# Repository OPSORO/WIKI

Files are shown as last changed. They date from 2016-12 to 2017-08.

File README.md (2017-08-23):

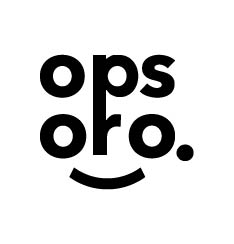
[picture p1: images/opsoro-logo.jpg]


# Welcome!

Welcome to the documentation wiki for OPSORO - open platform for social
robotics! This wiki is meant to guide you through the whole process of making
your own social robot(s).

* If you want more information about OPSORO, please visit our [website](https://www.opsoro.be/).
* If you have any questions, please visit our [forum](https://www.opsoro.be/forum/).
* You will find all necessary design files on our OPSORO [GitHub](https://github.com/OPSORO/) account.
* This wiki/book is licensed under the Creative Commons Attribution-ShareAlike 4.0 license.
* The OPSORO documentation was last updated in August 2017.

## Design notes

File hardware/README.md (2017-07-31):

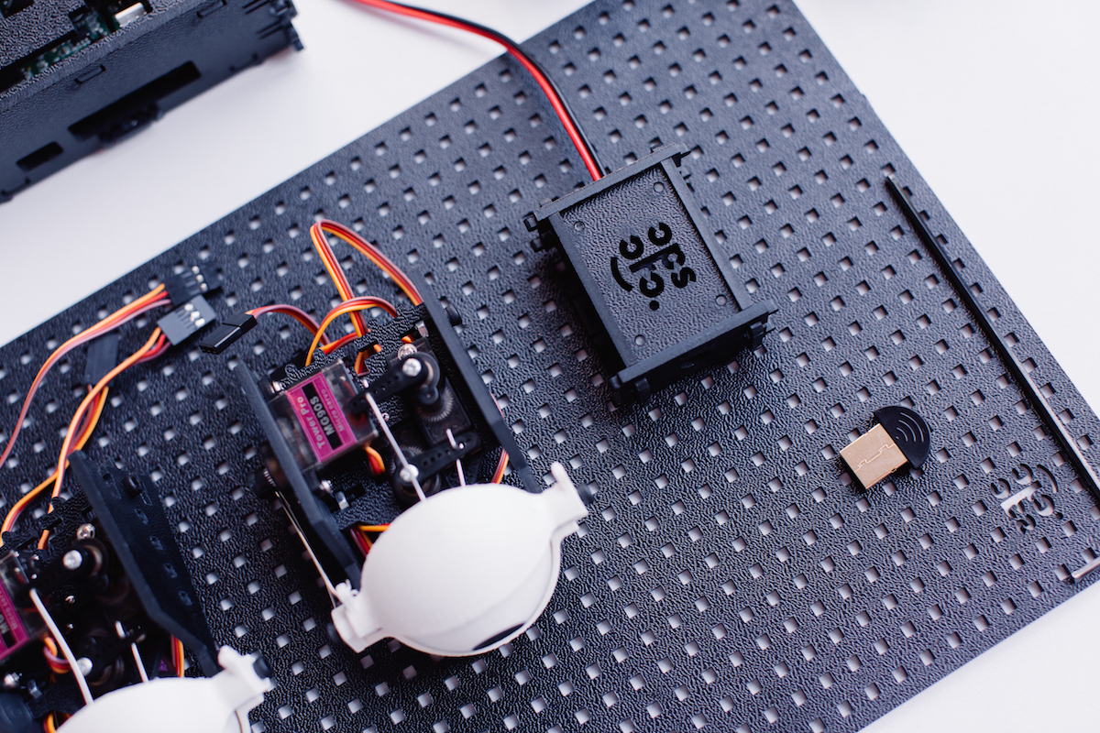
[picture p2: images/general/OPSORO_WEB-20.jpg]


# Hardware
This chapter describes all the hardware components of the Opsoro platform.
This includes general background information, technical details of the
electronics, module assembly guides, as well as instructions to build complete
social robots.

The source files for all the hardware components can be found on GitHub inside
the [OPSORO/BUILD](https://github.com/opsoro/build) repository. The OPSORO
hardware components are manufactured using laser-cutting and 3D-printing,
manufacturing techniques that are commonly found in fablabs and universities.
The designs are primarily created using [Rhinoceros](http://www.rhino3d.com),
though the repository also contains the appropriate derivative files
(e.g. STL, DXF).

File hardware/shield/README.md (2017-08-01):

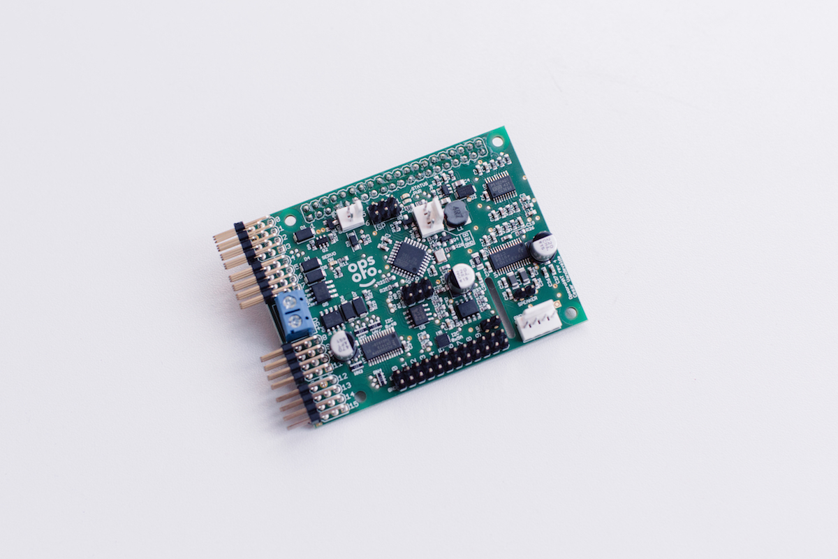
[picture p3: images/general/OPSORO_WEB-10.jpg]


# OpsoroHAT
OpsoroHAT is an add-on board for Raspberry Pi created specifically for building
DIY social robots. The board attaches on top of a standard Raspberry Pi,
allowing it to perform robot-specific tasks such as driving servo motors and
reading servos. The OpsoroHAT board can:
* drive up to 16 hobby servos
* drive a single 5W speaker
* read 12 capacitive touch inputs
* read 4 analog inputs

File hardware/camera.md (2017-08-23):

{% extends "./assembly-steps-template.md" %}

{% block heroimage %}
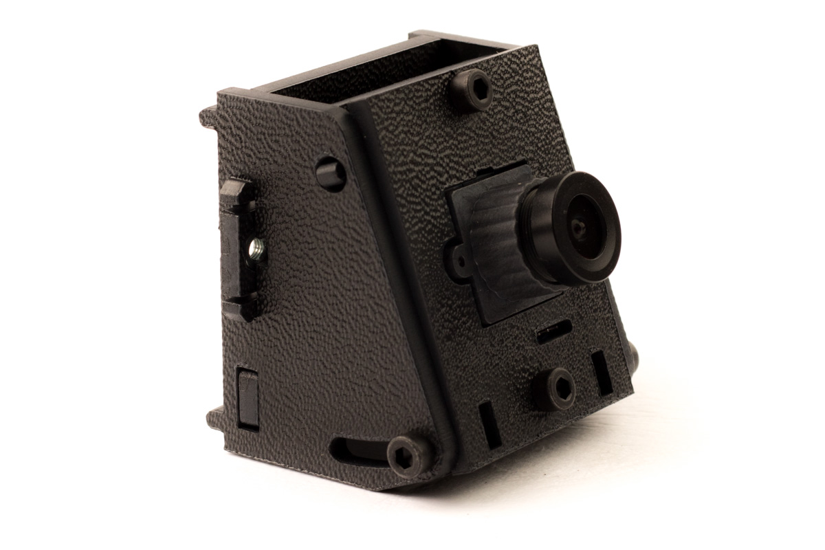
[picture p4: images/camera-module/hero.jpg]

{% endblock %}

{% block title %}Camera module{% endblock %}

{% block intro %}
The camera module gives your Opsoro robot the ability to see! Useful for all
sorts of computer vision applications, such as motion detection or face
recognition. The camera has a wide field of view and the tilt can be adjusted by
approximately 30°.
{% endblock %}

{% block parts %}
* 1 set of [laser-cut plastic parts](./appendix/custom-components.md#camera-module) (6 pieces)
* 4&times; [M3 nuts](./appendix/vendor-components.md#fasteners)
* 4&times; [M3x10 cap screws](./appendix/vendor-components.md#fasteners)
* 1&times; USB camera module
{% endblock %}

{% block tools %}
* [hex key 2.5mm](./appendix/tools.md#hex-key)
* diagonal cutters
{% endblock %}

{% set model = false %}

{% block steps %}
{{ super() }}

### Step 1
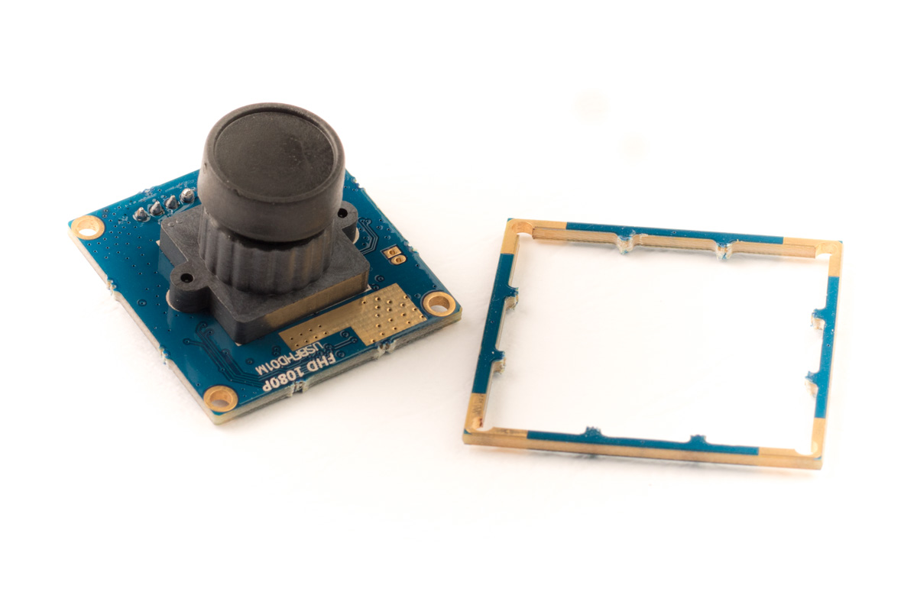
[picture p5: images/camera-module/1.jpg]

Use diagonal cutters to remove the border from the rest of the camera printed
circuit board.

### Step 2
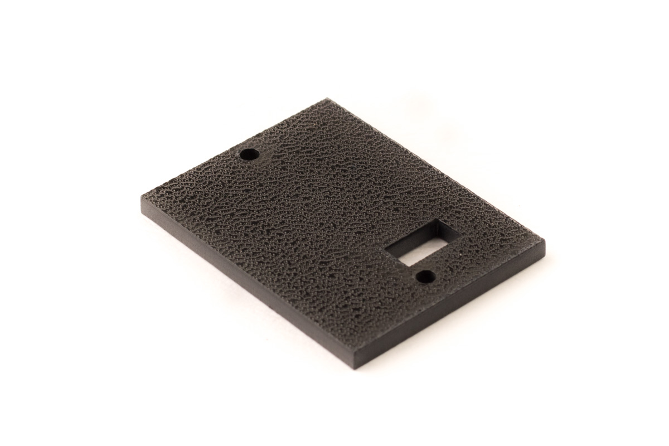
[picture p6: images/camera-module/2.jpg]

Start with the back plate. Mind the orientation of the rectangular opening.

### Step 3
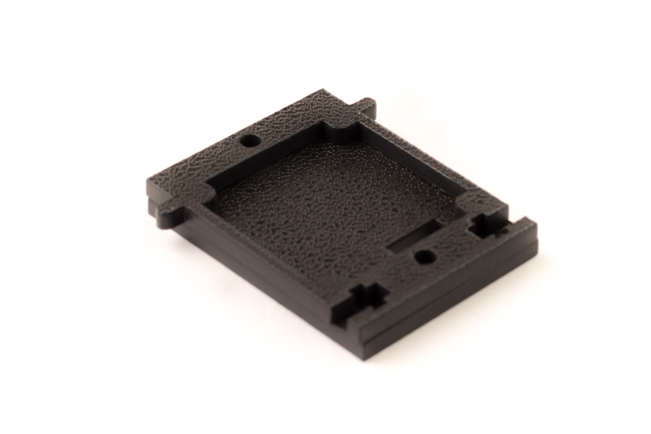
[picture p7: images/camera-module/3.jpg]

Put the mid plate on top of it. Again, mind the orientation.

### Step 4
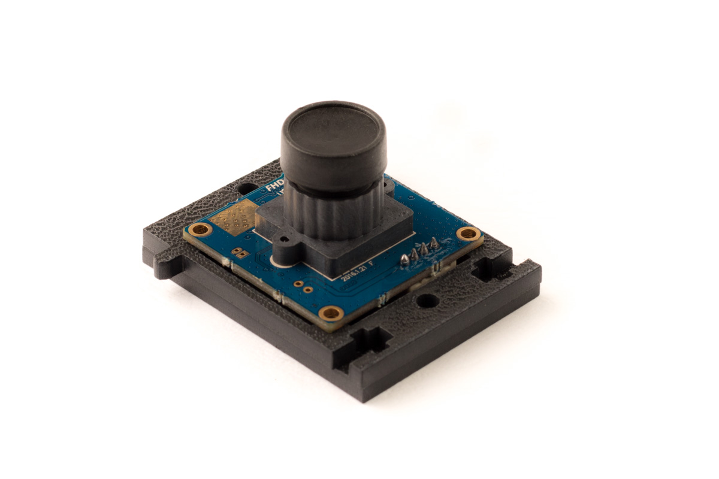
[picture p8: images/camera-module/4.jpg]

Put the camera PCB on top of the mid plate. The camera connector should fit in
the rectangular opening of the bottom plate.

### Step 5
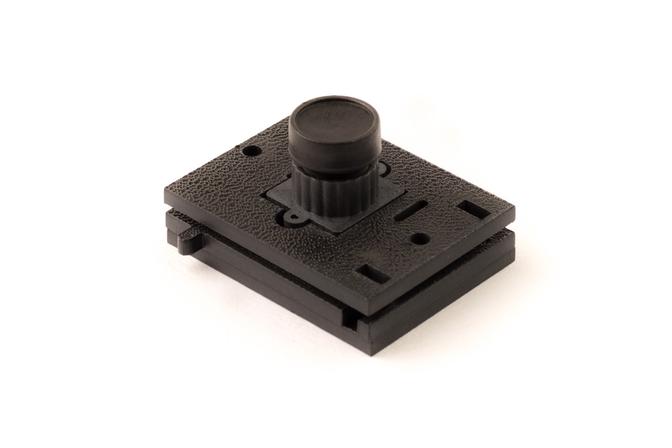
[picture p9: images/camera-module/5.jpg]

Put the top plate over the camera. Mind the orientation of the small slot, this
should fit over the pins of the connector.

### Step 6
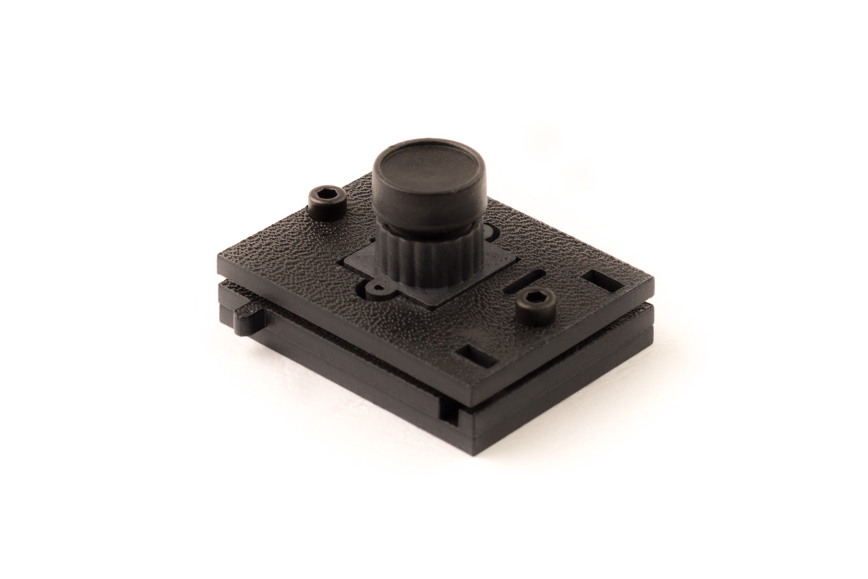
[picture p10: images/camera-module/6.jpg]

Secure everything in place using two M3x10 screws. They should screw directly
into the bottom plate.

> **Warning** Do not over-tighten the screws. Plastic threads are not as strong
> as metal threads.

### Step 7
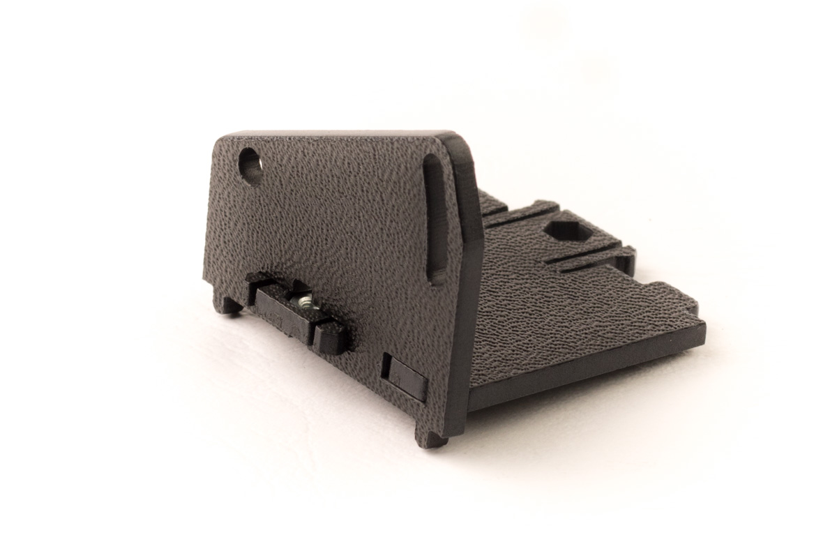
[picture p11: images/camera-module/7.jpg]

Insert an M3 nut into the back frame plate of the module. Clip the side frame
plate into position to secure the nut in place.

### Step 8
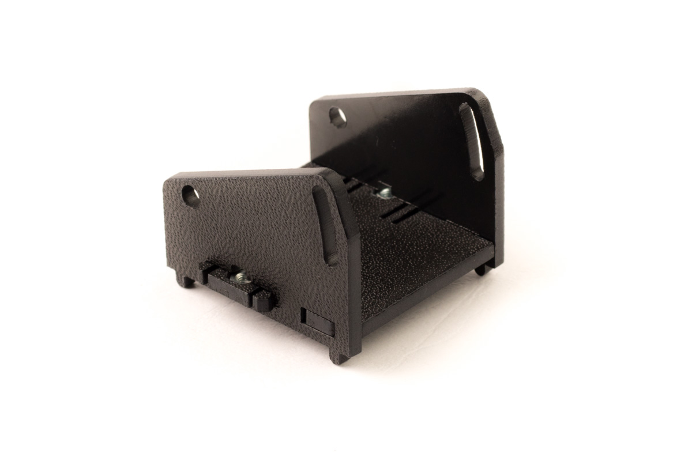
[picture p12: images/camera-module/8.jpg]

Repeat the same for the opposite side of the frame.

### Step 9
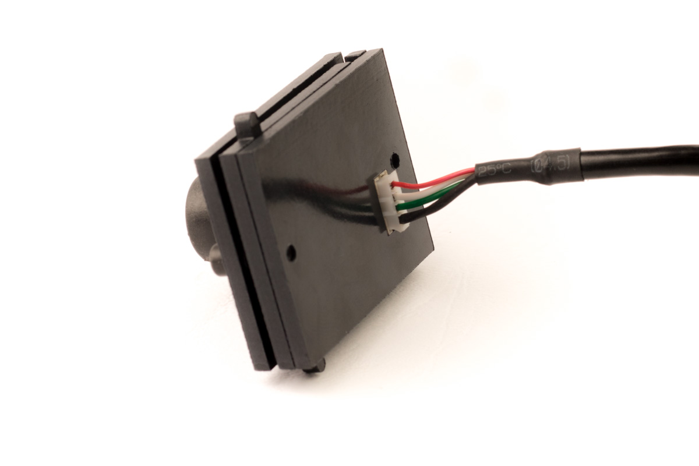
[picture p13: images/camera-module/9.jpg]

Attach the cable to the connector at the back of the camera PCB.

> **Info** The connector is keyed, so there's only one way to connect the cable.

### Step 10
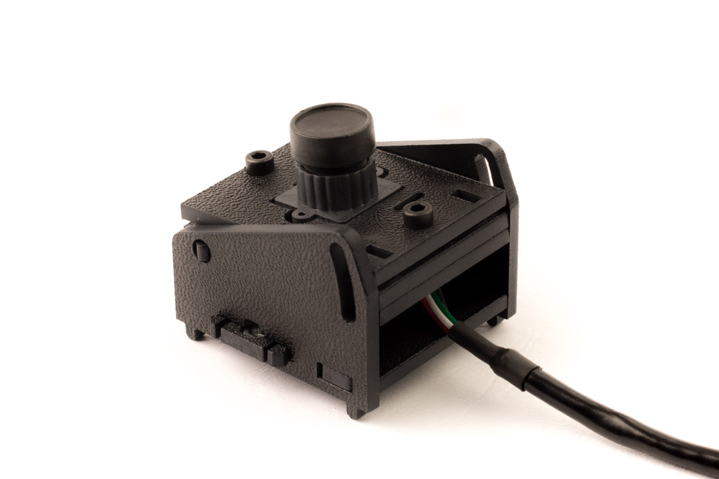
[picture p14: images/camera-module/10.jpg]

Slip the camera board subassembly into the module frame.

### Step 11
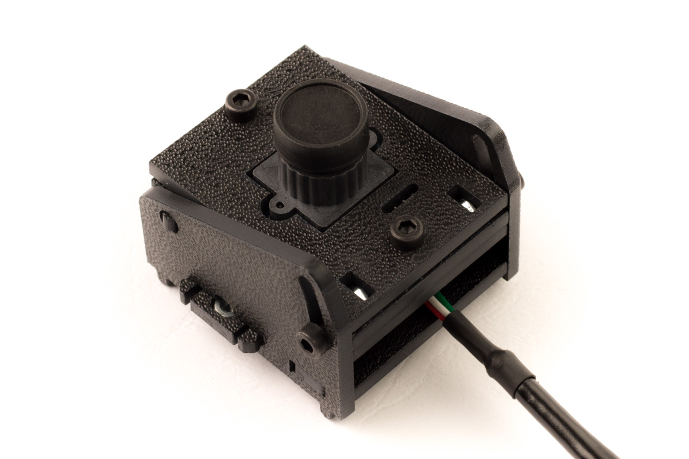
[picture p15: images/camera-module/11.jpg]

Insert two M3 nuts into the rectangular openings in front of the module. Secure
them in place using two M3x10 screws at the sides of the module. These two
screws allow you to adjust the tilt angle of the module. The camera module is
now ready for use!

{% endblock %}

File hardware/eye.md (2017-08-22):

{% extends "./assembly-steps-template.md" %}

{% block heroimage %}
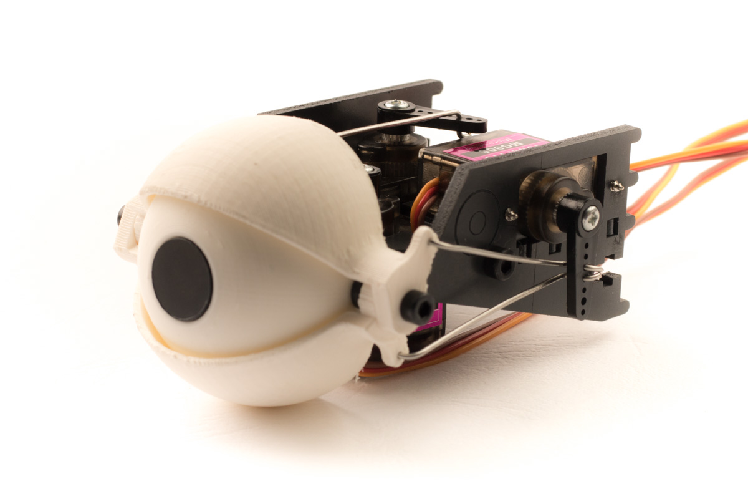
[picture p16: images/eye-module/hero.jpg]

{% endblock %}

{% block title %}Eye module{% endblock %}

{% block intro %}
The eye module is one of the most complex modules of the Opsoro platform. It
implements a 3-DOF eyeball in a small and compact package. The eyeball itself
can move up/down and left/right. The eyelids of the module are actuated by a
single servo. The eye module can be attached to the grid using a single M3x10
cap screw. Assembling this module can be tricky, so we advise you to take your
time and to read the instructions carefully.
{% endblock %}

{% block parts %}
* 1 set of [laser-cut plastic parts](./appendix/custom-components.md#eye-module) (5 pieces)
* 1&times; [eye shell](./appendix/custom-components.md#eye-shell) (printed)
* 1&times; [pivot beam](./appendix/custom-components.md#pivot-beam) (printed)
* 2&times; [eyelid](./appendix/custom-components.md#eyelid) (printed)
* 3&times; [micro servo set](./appendix/vendor-components.md#servos)
* 2&times; [M3x6 cap screws](./appendix/vendor-components.md#fasteners)
* 5&times; [M3x10 cap screws](./appendix/vendor-components.md#fasteners)
* 6&times; [M3 nuts](./appendix/vendor-components.md#fasteners)
* 4&times; [M3 washers](./appendix/vendor-components.md#fasteners)
* 20cm of 1mm steel wire
{% endblock %}

{% block tools %}
* [hex key 2.5mm](./appendix/tools.md#hex-key)
* small Philips screwdriver
* small needle-nose pliers
* diagonal cutters
{% endblock %}

{% set model = false %}
{% block model %}/assets/iris/eye_full test.iris/index.html{% endblock %}

{% block steps %}
## Preparation

### Step 1
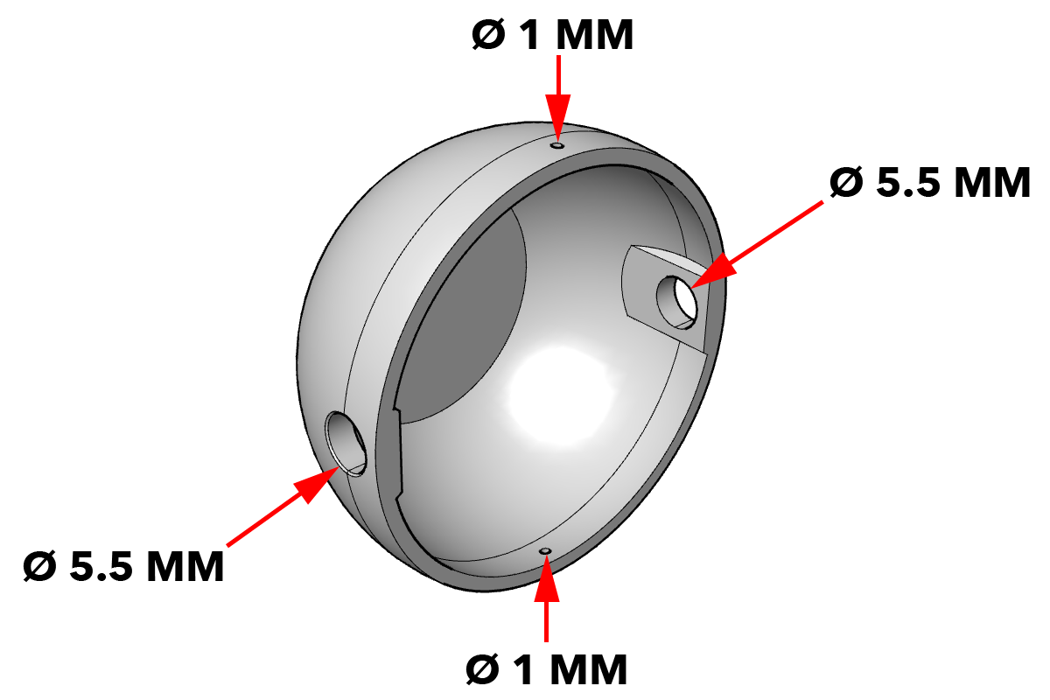
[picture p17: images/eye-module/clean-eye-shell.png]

Clean and deburr the 3D-printed eye shell. Use a cordless drill to drill out the
holes to the specified dimensions, as shown in the figure. Deburr the edges of
all the holes and use a file to remove any remaining print defects.

### Step 2
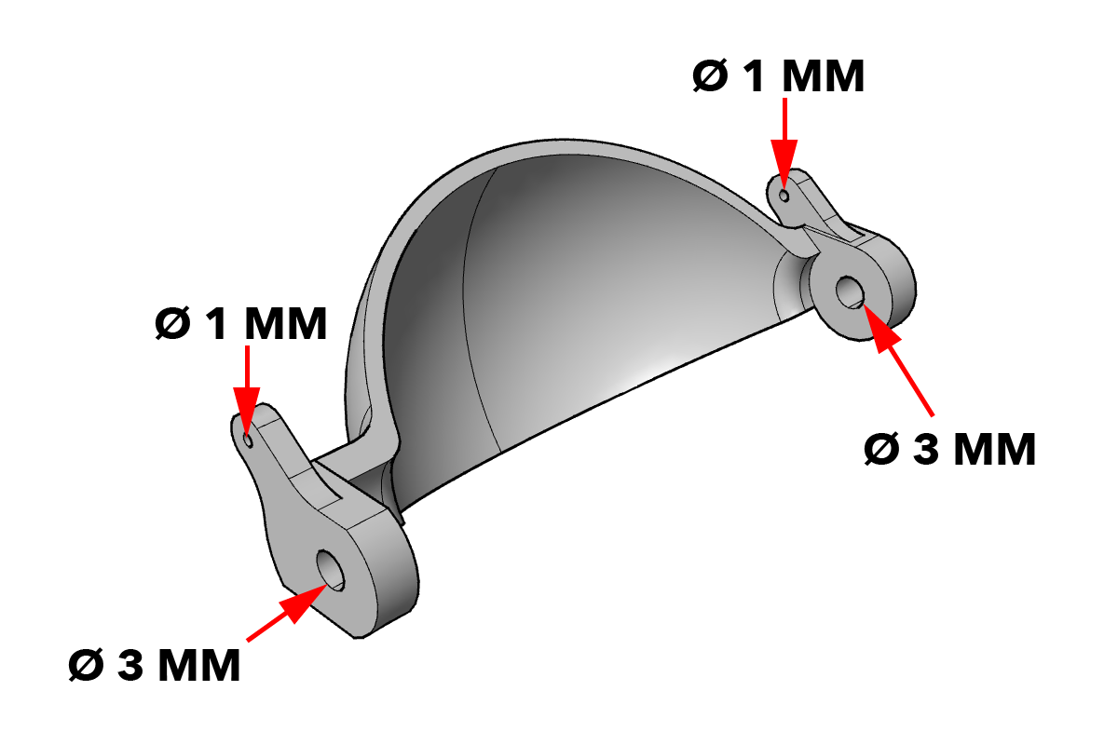
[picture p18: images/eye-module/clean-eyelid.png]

Use diagonal cutters to remove the support from the two 3D-printed eyelids.
Clean and deburr the two parts. Use a cordless drill to drill out the holes to
the specified dimensions, as shown in the figure. Deburr the edges of all the
holes and use a file to remove any remaining print defects.

> **Warning** The eye module requires two eyelids, so be sure to do this step twice.

### Step 1
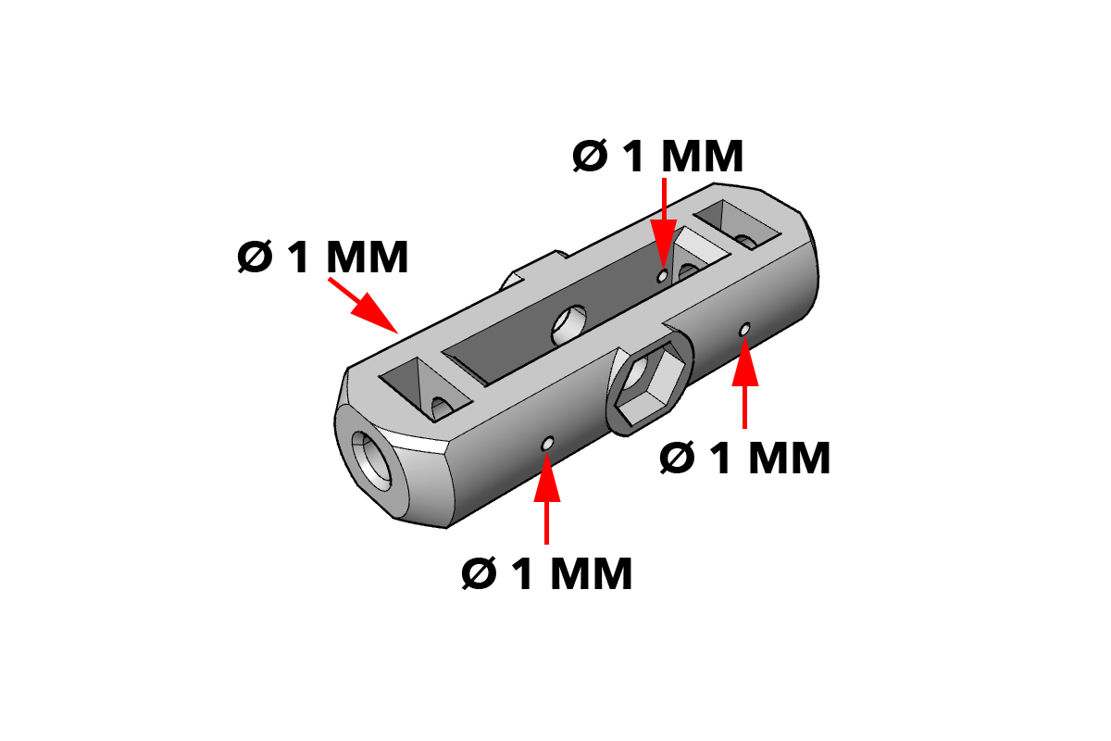
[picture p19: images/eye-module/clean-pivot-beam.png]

Clean and deburr the 3D-printed pivot beam. Use a cordless drill to drill out the
holes to the specified dimensions, as shown in the figure.

### Step 4
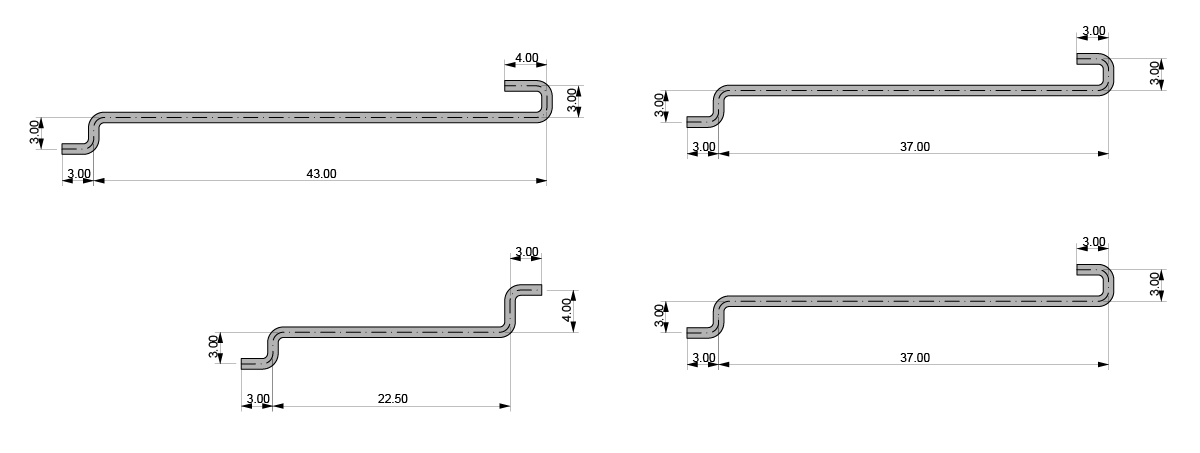
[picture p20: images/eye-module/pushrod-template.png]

Using a pair of needle-nose pliers and a pair of flush cutters, bend the 0.8mm
steel wire to form the four push rods of the module. Use the template above as a
guide.

> **Info** Print out the drawing at 1:1 scale. The PDF of the drawing can be
> found [here](https://github.com/OPSORO/BUILD/blob/master/modules/eye/extras/eye_wires.pdf).

### Step 5
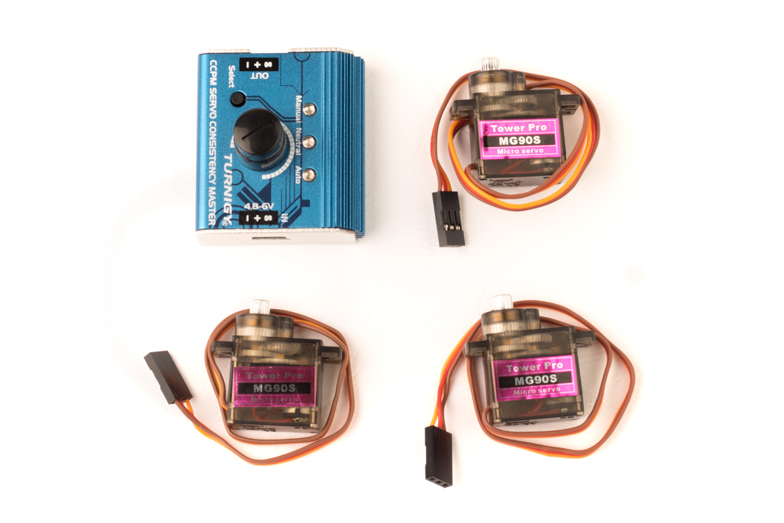
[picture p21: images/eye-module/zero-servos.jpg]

Use a servo tester to set the three servos to their neutral position. The
process is described [here](./appendix/centering-a-servo.md).

### Step 6
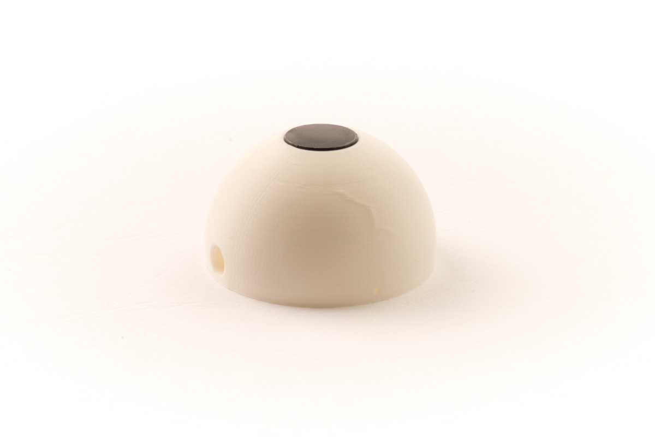
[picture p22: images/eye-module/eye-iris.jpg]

Insert the laser-cut iris into the eye shell. The iris should snap into place
and should be flush with the surface of the eye shell.

> **Info** Some force may be required to snap the iris in place. The easiest
> method is to put the iris down on a table and push the eye shell over it,
> pushing with your thumb from the inside of the eye shell.

## Assembly instructions

### Step 1
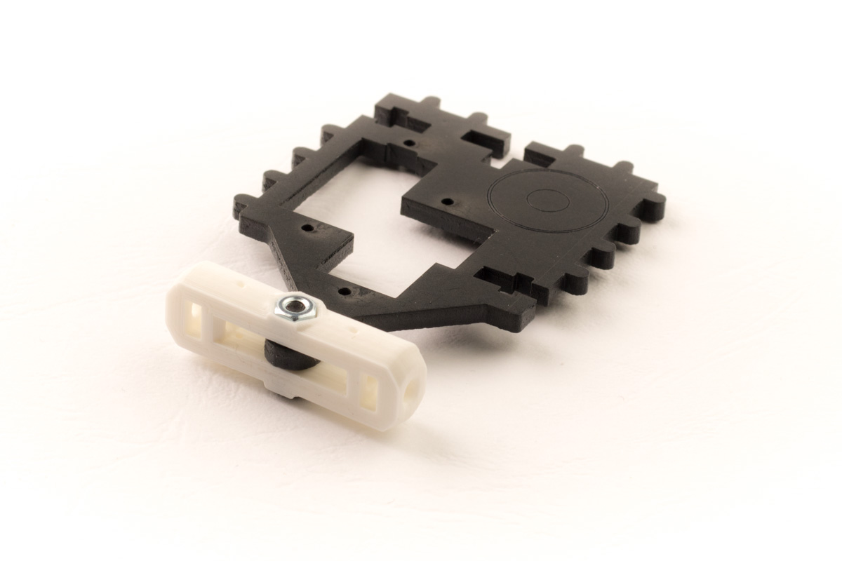
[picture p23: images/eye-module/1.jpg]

Attach the pivot beam to the mid plate using an M3x10 screw, an M3 nut, and two
M3 washers:
- Start by inserting the nut into the hexagonal opening of the pivot
beam.
- Insert the tip of the M3x10 screw through the opposite hole.
- Slip a washer over the tip of the screw
- Insert the mid plate
- Slip another washer over the tip of the screw
- Fasten the screw into the nut

> **Warning** Make sure you add the two washers. They are needed to create a
> low-friction pivot point. Do not over-tighten the screw, make sure that the
> pivot beam can turn freely.

### Step 2
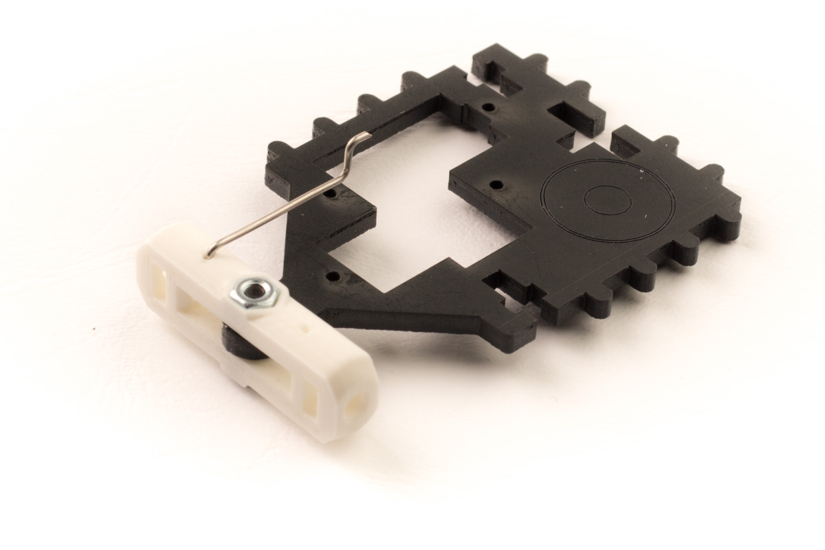
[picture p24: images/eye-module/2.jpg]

Attach the shortest push rod to pivot beam. Use needle-nose pliers to insert the
wire into the correct hole.

> **Warning** There are two holes in the pivot beam. Pick the one to the left,
> as shown in the picture.

### Step 3
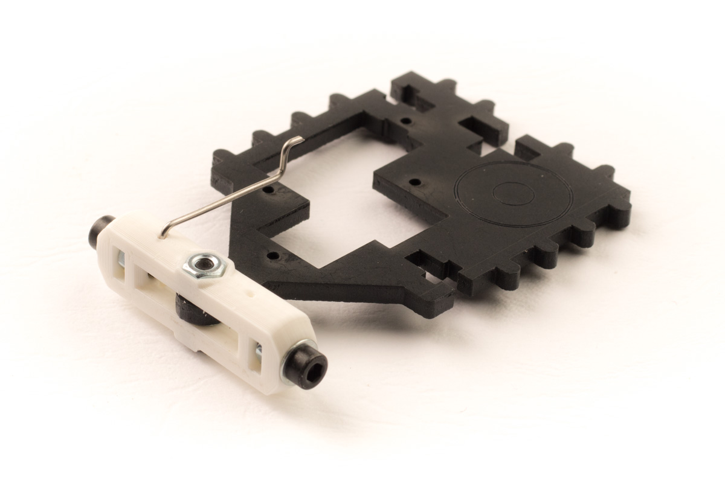
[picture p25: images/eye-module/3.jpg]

Insert an M3 nut into the rectangular opening of the pivot beam, then add a
washer on the opposite side and secure everything in place with an M3x10 screw.
Repeat the same process for the opposite side. The screw heads of the M3x10
screws will serve as the pivot point for the eye shell.

### Step 4

Attach a micro servo to the mid plate using the two included screws. Mind the
position and orientation of the servo.

> **Info** The servo should be inserted *from the bottom* of the module. The shaft
> of the servo should face *the front* of the module.

### Step 5

Attach the push rod to a servo horn. The rod should slip through the third hole
(counting from the tip). Then, attach the servo horn to the servo and secure it
in place using the included screw.

> **Warning** Make sure the servo is centered before attaching the servo horn.

### Step 6

Attach the second servo to the mid plate. Position the servo as shown in the
picture.

> **Info** The servo should be inserted **from the top** of the module. The shaft
> of the servo should face **the back** of the module.

### Step 7

Attach the eye shell to the pivot beam by squishing it slightly, and then
slipping it over the cap screw heads of the pivot beam. Make sure the eye shell
can rotate freely.

### Step 8

Attach the longest push rod to the top hole of the eye shell. Squish the end of
the push rod with needle-nose pliers so that the push rod is completely flush
with the surface of the eye shell.

### Step 9

Slip the other end of the push rod through a servo horn. The rod should be
attached to the third hole, counting from the tip. Attach the servo horn to the
servo's output shaft using the included screw.

### Step 10

Insert an M3 nut into the back clip component, then snap the back clip and the
nut into the mid plate of the module.

### Step 11

Attach the side plate **without opening** to the mid plate using an M3 nut and an
M3x10 screw. Mind the orientation of the component.

> **Warning** The horizontal edge of the side plate should be on the top side of
> the module. The side plate should be connected on right next to the servo.

### Step 12

Attach a servo to the remaining side plate, as shown in the picture. The servo
should be attached from the back of the of the plate and the servo's output
shaft should be oriented towards the front of the module.

> **Warning** Make sure the servo is centered before attaching the servo horn.

### Step 13

Slip the cable of the servo through the rectangular opening of the mid plate.
Then, attach the side plate to the rest of the module using an M3 nut and an
M3x10 screw.

### Step 14

There should be two remaining push rods. Attach one of them to the **short** end
of an eyelid. Attach the other to the **long** end of the other eyelid. The push
rods should be able to rotate freely.

> **Info** The eyelids are asymmetrical, the hinge feature of the eyelid is shorter
on one side and longer on the other side. Because of this, the same part can be
used for both upper and lower eyelid.

## Step 15

Attach the eyelids to the frame of the module using two M3x10 screws. Mind the
orientation of the eyelids:
- The long hinge of one eyelid should overlap with the short hinge of the other
  eyelid.
- The levers on the eyelids should be pointing backwards.
- The push rods should be located on the side of the servo.

## Step 16

Slip the ends of the push rods through the fourth and fifth hole of a servo horn
(counting from the tip). Attach the servo horn to the servo using the included
screw. Congratulations, the eye module is now ready!

{% endblock %}

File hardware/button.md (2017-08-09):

{% extends "./assembly-steps-template.md" %}

{% block heroimage %}

{% endblock %}

{% block title %}Button module{% endblock %}

{% block intro %}
A module with a big, *BIG* red button. What will happen when you push it?
You decide! The button module attaches to the grid via two M3x10 cap scews.
After connecting the cable to the OpsoroHAT, the button can be accessed directly
in Blockly and in other apps.
{% endblock %}

{% block parts %}
* 1 set of [laser-cut plastic parts](./appendix/custom-components.md#button-module) (6 pieces)
* 6&times; [M3 nuts](./appendix/vendor-components.md#fasteners)
* 1&times; [60mm arcade button](https://www.adafruit.com/product/1190)
* 1&times; red wire (20 cm)
* 1&times; yellow wire (20 cm)
* 1&times; black wire (20 cm)
* 1&times; resistor 10 k&#8486;
* 3&times; [DuPont crimp contact](./appendix/vendor-components.md#dupont-connectors)
* 1&times; [DuPont 2x3 connector housing](./appendix/vendor-components.md#dupont-connectors)
* Heat-shrink tubing (&empty; 6.4 mm)
{% endblock %}

{% block tools %}
* [hex key 2.5mm](./appendix/tools.md#hex-key)
* [wire strippers](./appendix/tools.md#stripper)
* [DuPont crimping tool](./appendix/tools.md#dupont)
* [soldering iron](./appendix/tools.md#soldering-iron)
{% endblock %}

{% set model = false %}
{% block model %}/assets/iris/eye_full test.iris/index.html{% endblock %}

{% block steps %}
{{ super() }}

### Step 1

Remove the microswitch from the button assembly by twisting the switch
counter-clockwise.

### Step 2

Cut off a piece of red, yellow, and black wire. Strip off both ends of the
wires.

### Step 3

Trim the lead of a 10K resistor and solder it to the black wire.

### Step 4

Solder the other end of the resistor to the bottom terminal of the switch.
Solder the yellow wire to this terminal as well.

### Step 5

Slip a piece of heat-shrink tubing over the connector tab and heat it up to
shrink it in place.

### Step 6

Solder the red wire to the middle connector tab of the microswitch.

### Step 7

Slip a piece of heat-shrink tubing over the solder joint and heat it up in
place.

### Step 8 (optional)

**Optional:** Use a cordless drill to twist the wires together.

### Step 9

Using a dupont crimp tool, attach three crimp connectors to one end of the
cable.

### Step 10

Insert the crimp connectors into the crimp housing. Mind the orientation of the
little barb on the crimp connector. Push until you hear it click into position.

> **Warning** Pay close attention to the position of each wire in the
> connector housing!

### Step 11

Insert the top of the button assembly into the top plate of the module. Secure
the button top in place with the included plastic nut.

### Step 12

Reassemble the button assembly by attaching the microswitch to the button top.

### Step 13

Take the bottom plate and insert an M3 nut in one of the hexagonal openings.
Snap a side plate (with snap connectors) onto the bottom plate so that it holds
the M3 nut in place.

### Step 14

Slide the top plate with the button assembly into place. Then, insert another M3
nut in the hexagonal opening of the bottom place and secure it in place by
snapping the opposite side plate into place.

### Step 15

Insert two M3 nuts into the hexagonal openings on one side of the module. Secure
the nuts into place by attaching one of the remaining side plate (the one
without cable opening).

### Step 16

Take the remaining side plate and slide it over the cable via the cable opening.

### Step 17

Insert two M3 nuts into the hexagonal holes, then snap the final side plate into
position. The module is done!

{% endblock %}

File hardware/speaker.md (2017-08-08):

{% extends "./assembly-steps-template.md" %}

{% block heroimage %}
  
{% endblock %}

{% block title %}Speaker module{% endblock %}

{% block intro %}
The speaker module houses a miniature 4W speaker which can be attached directly
to the speaker output of the OpsoroHAT. The module can be mounted either
straight or perpendicular to the grid using two M3x10 cap screws.
{% endblock %}

{% block parts %}
* 1 set of [laser-cut plastic parts](./appendix/custom-components.md#speaker-module) (6 pieces)
* 4&times; [M3x6 cap screws](./appendix/vendor-components.md#fasteners)
* 6&times; [M3 nuts](./appendix/vendor-components.md#fasteners)
* 1&times; [miniature 4 Ohm 4W speaker](./appendix/vendor-components.md#speaker)
* 40cm of speaker cable
* 2&times; [dupont crimp connectors](./appendix/vendor-components.md#dupont-connectors)
* 1&times; [dupont 1x2 crimp housing](./appendix/vendor-components.md#dupont-connectors)
{% endblock %}

{% block tools %}
* [hex key 2.5mm](./appendix/tools.md#hex-key)
* [wire strippers](./appendix/tools.md#stripper)
* [DuPont crimping tool](./appendix/tools.md#dupont)
* [soldering iron](./appendix/tools.md#soldering-iron)
{% endblock %}

{% set model = false %}
{% block model %}/assets/iris/eye_full test.iris/index.html{% endblock %}

{% block steps %}
{{ super() }}

### Step 1

Strip the insulation from both ends of the wire. Split the two conductors over a
distance of 1cm on both ends.

### Step 2

Using a dupont crimp tool, attach two crimp connectors to one end of the cable.

### Step 3

Insert the crimp connectors into the crimp housing. Mind the orientation of the
little barb on the crimp connector. Push until you hear it click into position.

### Step 4

Tin the ends of cable, then solder them to the tabs of the miniature speaker.
The polarity of the wires does not matter.

### Step 5

Attach the miniature speaker to the front plate of the speaker module using four
M3x6 cap screws. The screws attach from the back so that the screw heads are
hidden inside once the module is finished.

### Step 6

Insert an M3 nut into the hexagonal hole of the bottom plate. Snap the side
plate onto the bottom plate so that the nut stays in place.

### Step 7

Slide the top place (with speaker attached) into place.

### Step 8

Insert another M3 nut into the bottom place, and then snap the second side plate
onto the bottom plate.

### Step 9

Insert two M3 nuts into the hexagonal openings of the side plates, and then snap
the short side plate into place.

> **Hint** A spare M3 screw can be handy to keep the nuts in place while you
> maneuver the plate into place.

### Step 10

Insert the speaker cable through the circular opening in the remaining side
plate.

### Step 11

Snap the remaining side plate into place. The module is now ready for use!

{% endblock %}

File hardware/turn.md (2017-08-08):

{% extends "./assembly-steps-template.md" %}

{% block heroimage %}
  
{% endblock %}

{% block title %}Turn module{% endblock %}

{% block intro %}
The turn module contains a single micro-size servo motor, and can be used as a
general building block for designing social robots. For instance, the turn
module can be used to implement an eyebrow with a single DOF. The module can be
mounted either straight or perpendicular to the grid using 2 M3x10 cap screws.
{% endblock %}

{% block parts %}
* 1 set of [laser-cut parts](./appendix/custom-components.md#turn-module) (7 pieces)
* 3&times; [M3 nuts](./appendix/vendor-components.md#fasteners)
* 1&times; [micro servo set](./appendix/vendor-components.md#servos)
{% endblock %}

{% block tools %}
* [hex key 2.5mm](./appendix/tools.md#hex-key)
* small Philips screwdriver

*Optional:*
* [servo tester](./appendix/tools.md#servo-tester)
{% endblock %}

{% set model = false %}
{% block model %}/assets/iris/turn-module.iris/index.html{% endblock %}

{% block steps %}
{{ super() }}

### Step 1

Insert two M3 nuts into the small clips.

### Step 2

Snap the small clips into the side plates of the module.

### Step 3

Insert an M3 nut into the middle plate of the module.

### Step 4

Carefully slide the middle plate into the bottom plate, taking care that the
nut stays in place

### Step 5

Snap the side plate into position. Mind the orientation: the three protrusions
should be near the back plate.

### Step 6

Snap the top plate into place. The plate is asymmetric; the cutout for the servo
cable should be to the right, as shown in the picture.

### Step 7

Snap the other side-plate into place. Again, pay attention to the orientation of
the protrusions.

### Step 8

Insert the servo and attach it using the included screws. The cable of the servo
should be on the same side as the notch in the opening. The module is now ready
for use!

### Step 9 (optional)

**Optional:** Use the servo tester to put the servo in a neutral position, and then
attach the servo horn using the included screw.

{% endblock %}

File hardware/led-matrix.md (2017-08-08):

{% extends "./assembly-steps-template.md" %}

{% block heroimage %}

{% endblock %}

{% block title %}LED matrix module{% endblock %}

{% block intro %}
> **Warning** This module is still under development. Instructions are
> incomplete and the PCB design still needs work. Proceed with caution.

A module with a 8x8 pixel LED matrix display. The matrix itself is 32&times;32
mm large and multiple modules can be tiled together to form an arbitrarily large
display. The module can be attached to the grid using 2 M3x10 cap screws and
connects to the Raspberry Pi via USB.
{% endblock %}

{% block parts %}
* 1 set of [laser-cut plastic parts](./appendix/custom-components.md#led-matrix-module) (5 pieces)
* 2&times; [M3 nuts](./appendix/vendor-components.md#fasteners)
* 1&times; [LED matrix board](./appendix/custom-components.md#led-matrix-pcb)
* 1&times; micro USB cable
{% endblock %}

{% block tools %}
* [hex key 2.5mm](./appendix/tools.md#hex-key)
{% endblock %}

{% set model = false %}
{% block model %}/assets/iris/eye_full test.iris/index.html{% endblock %}

{% block steps %}
{{ super() }}

### Step 1

Insert two M3 nuts into the hexagonal holes in the bottom plate.

### Step 2

Slide the two smaller side-plates into the bottom plate.

### Step 3

Snap a big side-plate into place.

### Step 4

Do the same for the other side, completing the module's plastic frame.

### Step 5

Snap the LED matrix PCB into the module. The module is finished!

{% endblock %}

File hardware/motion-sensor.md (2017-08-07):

{% extends "./assembly-steps-template.md" %}

{% block heroimage %}

{% endblock %}

{% block title %}Motion sensor module{% endblock %}

{% block intro %}
> **Warning** This module is still under development. Instructions are
> incomplete so proceed with caution.

The module sensor module gives your robot the ability to detect motion near it.
The module uses a passive infrared sensor to sense people near it. This type of
sensor is very basic; it will only tell you that something is moving, but not
what is moving or where. The motion sensor module can be connected to the grid
using 2 M3x10 screws.
{% endblock %}

{% block parts %}
* 1 set of [laser-cut plastic parts](./appendix/custom-components.md#motion-sensor-module) (6 pieces)
* 2&times; [M3 nuts](./appendix/vendor-components.md#fasteners)
* 2&times; [M3x6 cap screws](./appendix/vendor-components.md#fasteners)
* 1&times; PIR motion sensor PCB
* 1&times; male/male servo cable (150mm)

{% endblock %}

{% block tools %}
* [hex key 2.5mm](./appendix/tools.md#hex-key)
{% endblock %}

{% set model = false %}
{% block model %}/assets/iris/eye_full test.iris/index.html{% endblock %}

{% block steps %}
{{ super() }}

### Step 1

Attach the PIR motion sensor to the front plate using two M3x6 screws. The sensor
should be attached from the back, so that the screw heads end up inside the
module and the white dome ends up on the outside.

### Step 2

A modified male/male servo cable is needed to connect the module. Take the cable
and swap the red and white wires on one end of the cable. Plug the modified into
the connector on the sensor PCB, as shown in the picture. Pay close attention to
the polarity of the cable!

### Step 3

Insert two M3 nuts into the hexagonal holes in the bottom plate.

### Step 4

Attach the side plates using the snap connectors.

### Step 5

There are two different side plates for this module, one with a cable opening
and one without. Attach the side plate _without_ cable opening.

### Step 6

Slide the top plate with attached sensor into the side plate.

### Step 7

Slip the cable through the cable opening in the remaining side plate.

### Step 8

Snap the side plate into place. The module is now ready!

{% endblock %}

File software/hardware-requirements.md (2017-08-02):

# Hardware Requirements

The following hardware is needed to use OpsoroOS:
* A Raspberry Pi
* An >8GB SD card
* An [OpsoroHAT][hat] (optional, but highly recommended)

OpsoroOS has been tested with the following single-board computers:
* Raspberry Pi 1 model B+
* Raspberry Pi 2 model B
* Raspberry Pi 3 model B

An [OpsoroHAT][hat] is required to make the software do
anything useful, though the software will run without it. OpsoroOS can be used
through a web interface over a WiFi network created by the Raspberry Pi. For
this, the Raspberry Pi needs to have WiFi connectivity. The Raspberry PI 3 has
built-in WiFi. For other boards, an external WiFi dongle must be used. We
recommend the [WiPi][wipi] dongle, though any dongle that supports AP-mode can
be used.

[wipi]: http://be.farnell.com/element14/wipi/dongle-wifi-usb-for-raspberry/dp/2133900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\
[hat]: /hardware/shield/

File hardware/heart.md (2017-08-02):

{% extends "./assembly-steps-template.md" %}

{% block heroimage %}

{% endblock %}

{% block title %}Heart module{% endblock %}

{% block intro %}
The heart module forms the core of an Opsoro robot: it is responsible for
bringing all the modules to life. The heart module houses the electronics of the
robot in a convenient form factor that can be attached to the [grid](grid.md).
It contains a Raspberry Pi 3 with an [OpsoroHAT](shield/README.md) attached to
it. A single barrel connector provides power to both the motors and the
controller.
{% endblock %}

{% block parts %}
* 1 set of laser-cut plastic parts (6 pieces)
* 2&times; laser-cut base spacer
* 4&times; M2.5x11 spacer
* 4&times; M2.5x20 cap screw
* 6&times; M3 nut
* 1&times; Raspberry Pi 3 model B
* 1&times; OpsoroHAT
* 1&times; panel mount 2.1mm DC barrel connector
* 1&times; 2-position Molex KK connector housing
* 2&times; Molex KK female crimp contact
* 2&times; cable ferrules
{% endblock %}

{% block tools %}
* hex key 2.5mm
* hex key 2mm
* [wire strippers](../hardware/tools.md#stripper)
* [DuPont crimping tool](../hardware/tools.md#dupont)
* ferrule crimping tool
* [soldering iron](../hardware/tools.md#soldering-iron)
{% endblock %}

{% set model = true %}
{% block model %}/assets/iris/eye_full test.iris/index.html{% endblock %}

{% block steps %}
{{ super() }}

### Step 1
Quisque et elit non enim fringilla cursus. Aliquam tortor erat, vestibulum vitae sagittis eget, pulvinar et ante. Sed at porttitor orci, ac porta dui.

### Step 2
Integer dictum eget quam in maximus. Nunc id porta mi, eget condimentum massa. Vestibulum eget iaculis libero. Mauris finibus posuere gravida.

### Step 3
Morbi nisi lectus, interdum sed sapien nec, interdum finibus turpis. Nunc luctus velit sed metus eleifend, quis dignissim ligula tincidunt.

{% endblock %}

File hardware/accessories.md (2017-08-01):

# Accessories

## A4 grid

## Cable clip

## Servo horn spacer

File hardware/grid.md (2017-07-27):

# The Opsoro grid
The Opsoro construction system is based around a grid system. Grid plates form
the backbone onto which the modules are attached. Modules can be attached to a
grid plate using a single M3x10 cap screw. The video below shows a quick
demonstration of this principle.

<video autoplay="" loop="" muted="" playsinline="" preload="true">
  <source src="/video/minigrid-demo.webm" type="video/webm">
  <source src="/video/minigrid-demo.mp4" type="video/mp4">
</video>

## Dimensions
The figure above shows the basic grid dimensions. The grid consists of
3mm &times; 3mm square holes, spaced at an 8mm interval. The design files for a
standard A4-sized grid can be found
[here](https://github.com/OPSORO/BUILD/tree/master/grid). The A4 grid can be
used as a starting point, however nothing is stopping you from creating
custom-sized grids.



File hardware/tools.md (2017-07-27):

# List of tools
The purpose is to give a visual overview of all tools needed to build Opsoro
robots. The various assembly guides reference this document in order to give
extra information on the various tools.

## Hex key {#hexkey}
Hex key 2.5mm
ball vs straight
aka allen wrench

## Servo tester {#servotester}

A servo tester is a small device that can be used to quickly test the
functionality of hobby servos. They are used for centering a servo and for
checking whether a servo is still working. Servo testers have three different
modes: manual, neutral, and sweep. Most servo testers do not come with a power
supply. In order to use a servo tester, you will need to attach a stable 5V
power source. One option is to use a lab power supply. Another option is to a
Dupont connector to an existing 5V adapter, such as an USB charger.

## Wire stripper {#stripper}

Wire strippers are used to remove the insulation from the end of wires so that
they may be soldered or crimped to.
We like using high-quality automatic wire strippers, though less expensive tools
are certainly serviceable as well! However, if you need to strip a lot of wires,
it might be advisable to invest in a good wire stripping tool.

## DuPont crimping tool {#dupont}

A crimping tool is a specialized hand tool that is used to attach metal contacts
to the end of a wire in order to attach a connector. A crimping tool is specific
to the type of connector used. We use DuPont connectors for most wiring. This
connector is compatible with 2.54mm pin headers and the crimping tool is cheap
and versatile. A DuPont crimping tool can be bought from various vendors
(e.g. [Adafruit](https://www.adafruit.com/product/1213)).
[This instructable](http://www.instructables.com/id/Dupont-Crimp-Tool-Tutorial/)
gives a good explanation of how to use a crimping tool to create custom cables.
Using a crimping tool takes a bit of practice to get right, so don't be
discouraged if you don't get the hang of it right away.

## Soldering iron {#soldering-iron}

A soldering iron is used to make permanent electrical connections using solder.
It is a versatile tool for any sort of electronics work. A simple pencil-style
iron can be bought for less than 20€. A temperature-controlled soldering station
is a bit more expensive, but offers better control and will make a difficult
soldering job much easier.

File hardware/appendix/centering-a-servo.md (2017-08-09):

# Centering a servo
Servos have a limited range of motion, typically somewhere between 120° and
180°. Because of the built-in potentiometer, they "remember" their position,
even when they are turned when they are not powered on. For these reasons, it is
necessary to *center a servo* before it is attached to a mechanism. This process
puts the the servo in its neutral position. This page describes how to achieve
this.

<div class="parts-tools">
  <div>
    {% md %}
#### Tools needed
* 5V power supply
* [Servo tester](tools.md#servo-tester)
* [Servo](vendor-components.md#servos)
    {% endmd %}
  </div>
</div>

## Step 1

You will need a suitable 5V power supply with a 2-pin
[DuPont connector](vendor-components.md#dupont-connectors) to power the servo
tester. If you have a lab power supply available, you can use that. Another
option is to use an old USB power supply. Cut off the micro USB connector, strip
the leads, and attach a DuPont connector.

## Step 2

Attach the power supply to the power input of the servo tester.

> **Warning** Mind the orientation of the connector. The red wire should be
> connected to the + pin, the black wire should be connected to the - pin, and
> the S pin should be left unconnected.

## Step 3

Press the *select* button once to put the tester in neutral mode.

## Step 4

Attach the servo to the servo tester. You should see the output shaft of the
servo move...

> **Warning** Mind the orientation of the connector. The brown wire should be
> connected to the - pin, the red wire should be connected to the + pin, and the
> orange wire should be connected to the S pin.

## Step 5 (Optional)

**Optional:** Now that the servo is in a neutral position, the servo horn can be
attached.

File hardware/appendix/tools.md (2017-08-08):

# List of tools
The purpose of this article is to give a visual overview of all tools needed to
build Opsoro robots. The various assembly guides reference this document in
order to give extra information on the various tools.

## Hex key

A hex key, also known as an allen wrench, is used to tighten or loosen hex
socket fasteners. Hex keys have the advantage that they are a bit easier to use
in tight spaces than a conventional screwdriver. A 2.5mm hex key is required for
using the Opsoro system.

## Servo tester

A servo tester is a small device that can be used to quickly test the
functionality of hobby servos. They are used for centering a servo and for
checking whether a servo is still working. Servo testers have three different
modes: manual, neutral, and sweep. Most servo testers do not come with a power
supply. In order to use a servo tester, you will need to attach a stable 5V
power source. One option is to use a lab power supply. Another option is to a
Dupont connector to an existing 5V adapter, such as an USB charger.

## Wire stripper {#stripper}

Wire strippers are used to remove the insulation from the end of wires so that
they may be soldered or crimped to.
We like using high-quality automatic wire strippers, though less expensive tools
are certainly serviceable as well! However, if you need to strip a lot of wires,
it might be advisable to invest in a good wire stripping tool.

## DuPont crimping tool {#dupont}

A crimping tool is a specialized hand tool that is used to attach metal contacts
to the end of a wire in order to attach a connector. A crimping tool is specific
to the type of connector used. We use DuPont connectors for most wiring. This
connector is compatible with 2.54mm pin headers and the crimping tool is cheap
and versatile. A DuPont crimping tool can be bought from various vendors
(e.g. [Adafruit](https://www.adafruit.com/product/1213)).
[This instructable](http://www.instructables.com/id/Dupont-Crimp-Tool-Tutorial/)
gives a good explanation of how to use a crimping tool to create custom cables.
Using a crimping tool takes a bit of practice to get right, so don't be
discouraged if you don't get the hang of it right away.

## Soldering iron {#soldering-iron}

A soldering iron is used to make permanent electrical connections using solder.
It is a versatile tool for any sort of electronics work. A simple pencil-style
iron can be bought for less than 20€. A temperature-controlled soldering station
is a bit more expensive, but offers better control and will make a difficult
soldering job much easier.

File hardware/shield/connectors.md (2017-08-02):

# Connectors


## 1. Servo power input
Power input for servos and speaker. Connect to a beefy 5V power supply.
Pins are ground (top), and +5V (bottom).

## 2. Servo connectors
Numbered from 0 (top) to 15 (bottom). Pins are ground (left), power (middle),
and signal (right). Make sure servos are connected correctly! Ground is usually
colored black or brown, power is usually red, and signal is usually orange,
yellow, or white.

## 3. Raspberry Pi HAT connector
Connector to attach the board on top of a Raspberry Pi. The board also
provides power to the Raspberry Pi through this connector, so no separate USB
power supply is needed for the Pi.

## 4. Logic power input.
Connect to a separate 5V 2A power supply, do not use the
same power supply as the servos, as voltage drops from large current draws will
reset the Raspberry Pi. Pins are +5V (top) and ground (bottom).

## 5. ISP header
Used to flash firmware onto the board's ATMega328 microcontroller. A programmer is
needed for this, e.g. AVRISP mk2. This is normally done only once.

> **Warning** To program the OpsoroHAT, the board should be disconnected from
> the Raspberry Pi, and should be powered by an independent 3.3V power supply.
> The board can be powered in this way through connector 10.

## 6. NeoPixel connector
Used to attach [NeoPixel](http://www.adafruit.com/category/168) RGB LEDs. In
theory, the board supports up to 100 LEDs. However, more than a couple of LEDs
will require a separate power supply. Pins are:

| Location | Pin |
|---|---|
| top | data out |
| middle | +5V |
| bottom | ground |

## 7. Speaker output
The board is designed to drive a 4 ohm 5W speaker. 8 ohm
speakers can also be used, but the audio output will be quieter. The pins are
not polarized, orientation of the speaker does not matter.

## 8. I2C expansion port
Allows additional I2C devices, such as sensors or
[Grove I2C modules](http://www.seeedstudio.com/wiki/Grove_System), to be
connected to the board. The connector is level-shifted to 5V logic level.
Pins from left-to-right are:

| Location | Pin |
|---|---|
| left | ground |
| &nbsp; | +5V |
| &nbsp; | SDA |
| right | SCL |

## 9. EEPROM write-protect
Write-protect for the HAT identification EEPROM. Bridge this header
with a jumper to program the EEPROM. Currently not used.

## 10. Analog inputs
Allows the board to read up to 4 analog inputs (0 - 3.3V) using the
microcontroller's ADC. Possible sensors that could be
measured with this port include force-sensitive resistors,
light-dependent resistors, and potentiometers. Pins are:

| Location | Pin |
|---|---|
| top left | A2 |
| top middle | A0 |
| top right | 3.3v |
| bottom left | A3 |
| bottom middle | A1 |
| bottom right  | ground |

## 11. Capacitive touch inputs
Connect any electrically conductive material to these pins to create touch
sensors. The bottom row is connected to ground, this allows you to use shielded
wires. The electrodes should be connected on the top row. Electrode pins are
numbered 0 (left) to 11 (right).

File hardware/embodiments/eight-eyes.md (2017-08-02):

# Space Invader
{% extends "../assembly-steps-template.md" %}

{% block heroimage %}

{% endblock %}

{% block title %}Eight Eyes{% endblock %}

{% block intro %}
Eight Eyes is an installation that is designed to highlight the concept behind
the modular grid system. As the name implies, the design features eight separate
eye modules that are connected to a single, elongated grid plate. This grid
features the silhouettes of four distinct characters, hinting at the purpose of
Opsoro: using modular building blocks to bring social characters to life.
{% endblock %}

{% block parts %}
* 1 set of laser-cut plywood parts
  * 1&times; face (white)
  * 2&times; mouth (white)
  * 2&times; eyebrows (black)
* 6&times; laser-cut ABS spacers
* 1&times; [heart module](../heart.md)
* 1&times; [camera module](../camera.md)
* 8&times; [eye module](../eye.md)
* 6&times; M3 nut
* 10&times; M3x10 cap screws
* &plusmn; 10&times; [cable clip](../accessories.md#cable-clip)
* 10&times; [servo extension cable](../appendix/vendor-components.md)
{% endblock %}

{% block tools %}
* hex key 2.5mm
{% endblock %}

{% set model = false %}
{% block model %}/assets/iris/eye_full test.iris/index.html{% endblock %}

{% block steps %}
{{ super() }}

### Step 1
Quisque et elit non enim fringilla cursus. Aliquam tortor erat, vestibulum vitae sagittis eget, pulvinar et ante. Sed at porttitor orci, ac porta dui.

### Step 2
Integer dictum eget quam in maximus. Nunc id porta mi, eget condimentum massa. Vestibulum eget iaculis libero. Mauris finibus posuere gravida.

### Step 3
Morbi nisi lectus, interdum sed sapien nec, interdum finibus turpis. Nunc luctus velit sed metus eleifend, quis dignissim ligula tincidunt.

{% endblock %}

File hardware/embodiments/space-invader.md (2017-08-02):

# Space Invader
{% extends "../assembly-steps-template.md" %}

{% block heroimage %}

{% endblock %}

{% block title %}Space Invader{% endblock %}

{% block intro %}
Inspired by classical video games, the Space Invader has come to the physical
world in order to invade your personal space. The Space Invader is an example of
a minimal embodiment design for Opsoro. The invader shows that it only takes a
few laser-cut pieces of acrylic to transform a collection of modules into a
social character.
{% endblock %}

{% block parts %}
* 1 set of laser-cut acrylic parts
  * 1&times; face (white)
  * 2&times; mouth (white)
  * 2&times; eyebrows (black)
* 6&times; laser-cut ABS spacers
* 1&times; [A4 grid](../accessories.md#a4-grid)
* 1&times; [heart module](../heart.md)
* 1&times; [speaker module](../speaker.md)
* 4&times; [turn module](../turn.md)
* 2&times; [eye module](../eye.md)
* 6&times; M3 nut
* 10&times; M3x10 cap screws
* &plusmn; 10&times; [cable clip](../accessories.md#cable-clip)
* 10&times; [servo extension cable](../appendix/vendor-components.md)

*Optional:*
* 2&times; [LED matrix module](../led-matrix.md) *or*
* 1&times; [Button module](../button.md)
{% endblock %}

{% block tools %}
* hex key 2.5mm
{% endblock %}

{% set model = false %}
{% block model %}/assets/iris/eye_full test.iris/index.html{% endblock %}

{% block steps %}
{{ super() }}

### Step 1
Quisque et elit non enim fringilla cursus. Aliquam tortor erat, vestibulum vitae sagittis eget, pulvinar et ante. Sed at porttitor orci, ac porta dui.

### Step 2
Integer dictum eget quam in maximus. Nunc id porta mi, eget condimentum massa. Vestibulum eget iaculis libero. Mauris finibus posuere gravida.

### Step 3
Morbi nisi lectus, interdum sed sapien nec, interdum finibus turpis. Nunc luctus velit sed metus eleifend, quis dignissim ligula tincidunt.

{% endblock %}

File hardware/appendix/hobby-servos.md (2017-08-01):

# Using hobby servos
Hobby servos are used as the main actuators in Opsoro robots. These motors
originate from the RC world, where they are used to control model cars or
airplanes. These actuators have the advantage of being inexpensive and
relatively easy to control. However, when using these actuators, some things
need to be kept in mind:

* They have 3 wires: ground, 5V and signal. The servo will only work if these
wires are connected correctly. The colors of these wires can vary. Common color
codes include:
  * ground (brown), 5V (red), signal (orange)
  * ground (black), 5V (red), signal (white)

* Hobby servos have a limited range of motion. Usually, they are restricted to
180° of rotation. Beyond that, they hit a plastic tab inside the servo. These
actuators cannot be used for continuous rotation, but they can be told to rotate
to a certain position and stay in that position.

* To control them, a pulse-width modulation signal needs to be sent. The length
of the pulse determines the angle of the servo:

  * 500μs corresponds to minimum position (usually -90°)
  * 1500μs corresponds to neutral position (0°)
  * 2500μs corresponds to maximum position (usually +90°).

* The gearbox of the servo is internally connected to a potentiometer, which is
used to sense the position of the servo. As a result, it is important to first
put the servo in neutral position before connecting a mechanism to the output
shaft. Not doing so can result in unexpected behavior, such as the servo
destroying itself because it cannot rotate further.

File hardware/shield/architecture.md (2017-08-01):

# System architecture
> **Info** This article is intended for advanced users only.



The figure above shows a schematic overview of the OpsoroHAT electronics
architecture. The board has the following features:
* ATmega328 microcontroller which communicates with the Raspberry Pi over SPI.
* A 16 channel servo controller (PCA9685) with beefy power traces.
* A Power MOSFET to enable or disable all servos.
* An I2S soundcard with a 5W mono class-D amplifier, to be used with a 4 ohm or 8 ohm speaker.
* A 12 channel capacitive touch controller (MPR121).
* A power connector for back-powering the Raspberry Pi. (No more cutting up USB cables!)
* Support for NeoPixel LEDs
* A I2C expansion header with signals translated to 5V logic, convenient for hooking up arduino-compatible I2C devices
* A 4-channel analog sensor input.
* HAT EEPROM.
* Protection circuitry: TVS diodes, reverse polarity protection, etc.

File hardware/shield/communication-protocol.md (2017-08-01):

#Communication Protocol

> **Info** This article is intended for advanced users only.
> For most purposes, the HAT functionality can be accessed through the Opsoro API.

The Raspberry Pi communicates with the microcontroller on the OpsoroHAT via the
SPI bus. The SPI bus clock speed is set to a frequency of 122 kHz, this is the
maximum bus speed that the microcontroller can handle reliably. A typical
transaction between master (Raspberry Pi) and slave (OpsoroHAT) happens in two
phases.



The first step is to transfer a command plus its parameters (if any) to the
slave. Whenever the CS pin is pulled low by the master, the slave will interpret
the next MOSI byte as a command byte, with each consecutive byte stored in
buffer as parameter data. When the CS pin is driven to a logic high, the
microcontroller processes and executes the command, during which the master
waits. Results of commands, if any, are stored in an outgoing buffer.

The second step is to read the output of the command. This step is optional and
only occurs if the master is expecting return data. The CS pin is pulled to
logic low and a special CMD_READ byte is transferred to the slave. Each
subsequent byte sent by the master causes the slave to return the next byte of
the outgoing buffer.

## Command set

### General commands

| Command | Value | In | Out | Description |
|---|---|----|-----|---|
| CMD_NOP | 0 | 0  | 0 | No operation |
| CMD_NC | 255 | 0  | 0 | Not connected |
| CMD_PING | 1 | 0  | 1 | To check connection |
| CMD_READ | 2 | 0  | ? | Return result from previous command |
| CMD_RESET | 3 | 0  | 0 | Reset the ATmega328 |
| CMD_LEDON | 4 | 0  | 0 | Turn LED on |
| CMD_LEDOFF | 5 | 0  | 0 | Turn LED off |

### I2C commands

| Command | Value | In | Out | Description |
|---|---|----|-----|---|
| CMD_I2C_DETECT | 20 | 1  | 1 | Test if there's a device at address |
| CMD_I2C_READ8 | 21 | 2  | 1 | Read byte |
| CMD_I2C_WRITE8 | 22 | 3  | 0 | Write byte |
| CMD_I2C_READ16 | 23 | 2  | 2 | Read 2 bytes |
| CMD_I2C_WRITE16 | 24 | 4  | 0 | Write 2 bytes |

### Servo commands

| Command | Value | In | Out | Description |
|---|---|----|-----|---|
| CMD_SERVO_INIT | 40 | 0  | 0 | Init PCA9685 |
| CMD_SERVO_ENABLE | 41 | 0  | 0 | Turn on MOSFET |
| CMD_SERVO_DISABLE  | 42 | 0  | 0 | Turn off MOSFET |
| CMD_SERVO_NEUTRAL  | 43 | 0  | 0 | Set all servos to 1500 |
| CMD_SERVO_SET | 44 | 3  | 0 | Set 1 servo position |
| CMD_SERVO_SETALL | 45 | 32 | 0 | Set  position of all servos |

### Capacitive touch commands

| Command | Value | In | Out | Description |
|---|---|----|-----|---|
| CMD_CAP_INIT | 60 | 3  | 0 | Init MPR121 |
| CMD_CAP_SETTH | 61 | 3  | 0 | Set pin touch/release threshold |
| CMD_CAP_GETFD | 62 | 0  | 24  | Get pin filtered data (10 bits per electrode) |
| CMD_CAP_GETBD | 63 | 0  | 12  | Get pin baseline data, high 8 bits of 10 |
| CMD_CAP_TOUCHED | 64 | 0  | 2 | Get touched status |
| CMD_CAP_SETGPIO | 65 | 2  | 0 | Set GPIO mode |
| CMD_CAP_GPIOREAD | 66 | 0  | 1 | Read GPIO pin |
| CMD_CAP_GPIOWRITE  | 67 | 2  | 0 | Write GPIO pin |

### NeoPixel commands

| Command | Value | In | Out | Description |
|---|---|----|-----|---|
| CMD_NEO_INIT | 80 | 1  | 0 | Init Neopixel |
| CMD_NEO_ENABLE | 81 | 0  | 0 | Turn on MOSFET |
| CMD_NEO_DISABLE | 82 | 0  | 0 | Turn off MOSFET |
| CMD_NEO_SETBRIGHT  | 83 | 1  | 0 | Set brightness |
| CMD_NEO_SHOW | 84 | 0  | 0 | Show pixels |
| CMD_NEO_SET | 85 | 4  | 0 | Set single pixel |
| CMD_NEO_SETRANGE | 86 | 5  | 0 | Set range of pixels |
| CMD_NEO_SETALL | 87 | 3  | 0 | Set all pixels |
| CMD_NEO_SETHSV | 88 | 4  | 0 | Set single pixel HSV |
| CMD_NEO_SETRANGEHSV| 89 | 5  | 0 | Set range of pixels HSV |
| CMD_NEO_SETALLHSV  | 90 | 3  | 0 | Set all pixels HSV |

### Analog input commands

| Command | Value | In | Out | Description |
|---|---|----|-----|---|
| CMD_ANA_GET | 100 | 1  | 2 | Read an analog channel |
| CMD_ANA_GETALL | 101 | 0  | 8 | Read all analog channels |

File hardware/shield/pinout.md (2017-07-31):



#OpsoroHAT pinout
1. Power input for servos and speaker. Connect to a beefy 5V power supply.
Pins are ground (top), and +5V (bottom).

2. Connectors for RC servos. Numbered from 0 (top) to 15 (bottom). Pins are
ground (left), power (middle), and signal (right). Make sure servos are
connected correctly! Ground is usually colored black or brown, power is usually
red, and signal is usually orange, yellow, or white.

3. Connector to attach the board on top of a Raspberry Pi. The board also
provides power to the Raspberry Pi through this connector, so no separate USB
power supply is needed for the Pi.

4. Logic power input. Connect to a separate 5V 2A power supply, do not use the
same power supply as the servos, as voltage drops from large current draws will
reset the Raspberry Pi. Pins are +5V (top) and ground (bottom).

5. ISP header to program the board's ATMega328 microcontroller. A programmer is
needed for this, e.g. AVRISP mk2. This is normally only used once to program the
board's firmware. **Important:** To program the board, it should be disconnected
from the Raspberry Pi, and should be powered by an independent 3.3V power supply.
The board can be powered in this way through connector 10.

6. [NeoPixel](http://www.adafruit.com/category/168) connector. Pins are data out
(top), +5V (middle), ground (bottom). The board theoretically supports up to 100
LEDs, though a larger string of LEDs will require a separate power supply.

7. Speaker output. The board is designed to drive a 4 ohm 5W speaker. 8 ohm
speakers can also be used, but the audio output will be quieter. The pins are
not polarized, orientation of the speaker does not matter.

8. I2C port connector. Allows additional I2C devices, such as sensors or
[Grove I2C modules](http://www.seeedstudio.com/wiki/Grove_System), to be
connected to the board. The connector is level-shifted to 5V logic level.
Pins from left-to-right are ground, +5V, SDA, SCL.

9. Write-protect jumper for the HAT identification EEPROM, connect a jumper here
to program the EEPROM. Currently not used yet.

10. Analog sensor port. Allows the board to measure up to 4 analog signals
(0-3.3V) using the microcontroller's ADC. Possible sensors that could be
measured with this port include force-sensitive resistors,
light-dependent resistors, and potentiometers. Pins are:
  * A2 (top left)
  * A0 (top middle)
  * 3.3V (top right)
  * A3 (bottom left)
  * A1 (bottom middle)
  * ground (bottom right)

11. Connector for capacitive touch pads. Connect any electrically conductive
material to the pins on this connector to turn them into touch sensors. The
bottom row is connected to ground, this allows you to use shielded wires. The
electrodes should be connected on the top row. Electrode pins are numbered 0
(left) to 11 (right).

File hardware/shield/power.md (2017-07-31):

#Powering robots

## Single power supply

## Split power supply

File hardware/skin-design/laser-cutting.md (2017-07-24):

# Skin Design for Laser Cutting

<div style="display: flex; flex-direction: row;">
  <div style="flex-grow: 1;">
    <h4>Parts needed</h4>
    <ul>
      <li>Starter Kit</li>
      <li>Plate material</li>
      <li>ABC</li>
    </ul>
  </div>
  <div style="flex-grow: 1;">
    <h4>Tools needed</h4>
    <ul>
      <li>Laser Cutter</li>
      <li>Scissors</li>
      <li>Paper</li>
    </ul>
  </div>
</div>

<!-- toc -->

#### Digital Design
sdlkf

#### Lasering
sdlkf

#### Assembly
sdlkf

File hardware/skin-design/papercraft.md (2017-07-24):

# Papercraft Skinning

<div style="display: flex; flex-direction: row;">
  <div style="flex-grow: 1;">
    <h4>Parts needed</h4>
    <ul>
      <li>Starter Kit</li>
      <li>Paper</li>
      <li>ABC</li>
    </ul>
  </div>
  <div style="flex-grow: 1;">
    <h4>Tools needed</h4>
    <ul>
      <li>Color Printer</li>
      <li>Scissors</li>
      <li>Glue</li>
    </ul>
  </div>
</div>

<!-- toc -->

#### Print
Download available skins here " link to .pdf ".
Print the skin parts in full size.

#### Cut & Glue
Cut the marked lines and fold the thin edges where indicated. Apply glue and assemble the skin.

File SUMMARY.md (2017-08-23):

# Summary

## Getting started

* [Introduction](README.md)
* [About](getting-started/about.md)
* [FAQ](getting-started/faq.md)
* [Contribute](getting-started/contribute.md)

## Hardware

* [Introduction](hardware/README.md)
* [Grid](hardware/grid.md)
* Modules
  * [Turn](hardware/turn.md)
  * [Speaker](hardware/speaker.md)
  * [Heart](hardware/heart.md)
  * [Eye](hardware/eye.md)
  * [Button](hardware/button.md)
  * [LED matrix](hardware/led-matrix.md)
  * [Camera](hardware/camera.md)
  * [Motion sensor](hardware/motion-sensor.md)
* Embodiments
  * [Space Invader](hardware/embodiments/space-invader.md)
  * [Eight Eyes](hardware/embodiments/eight-eyes.md)
* [Accessories](hardware/accessories.md)
* [OpsoroHAT](hardware/shield/README.md)
  * [Overview](hardware/shield/README.md)
  * [Connectors](hardware/shield/connectors.md)
  * [Powering robots](hardware/shield/power.md)
  * [System architecture](hardware/shield/architecture.md)
  * [Communication Protocol](hardware/shield/communication-protocol.md)
* Appendix
  * [List of tools](hardware/appendix/tools.md)
  * [List of vendor components](hardware/appendix/vendor-components.md)
  * [List of custom components](hardware/appendix/custom-components.md)
  * [Using hobby servos](hardware/appendix/hobby-servos.md)
  * [Centering a servo](hardware/appendix/centering-a-servo.md)

## Software

* [Introduction](software/README.md)
* Installing OpsoroOS
  * [Hardware requirements](software/hardware-requirements.md)
  * [Installation](software/installation.md)
  * [Connecting via WiFi](software/connecting.md)
* Cloud platform
* Configuring your robot
* Apps
  * Preferences
  * Sound
  * Social script
  * Blockly
    * Examples
  * Lua Scripting
    * Examples

## Developers

* [Hardware module template](developers/hardware-module-template.md)
* [Software API](developers/api-documentation.md)

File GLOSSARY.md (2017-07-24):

## DOF
Degree of freedom

## PWM
Pulse-width modulation

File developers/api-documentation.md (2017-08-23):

# Software API

The Opsoro platform is designed to be easy to extend, both hardware-wise as well
as software-wise. The software platform borrows ideas from the app-paradigm on
smartphones and tablets, where the functionality of the software is split up
into task-specific apps. The Opsoro-OS comes with a number of default apps,
covering a variety of use basic use cases. However, this may not be enough for
everyone, so the true potential of the software can be unlocked by writing your
own custom app.

The source code of the Opsoro software can be found on GitHub inside
the [OPSORO/OS][repo] repository. The back-end of Opsoro software is written in
Python using the wonderful [Flask][flask] web framework. The front-end of the
software is built upon the [Foundation][fdn] framework. Interactive components
are created using [jQuery][jq] and [Knockout.js][ko].

An Opsoro app is a self-contained python module placed in the ```opsoro/apps/```
folder. This module contains python code, the HTML templates, and any other
required web assets. The software documentation of Opsoro is still
work-in-progress. A step-by-step tutorial to write an app is not yet available.
However, take a look at the [app template][app-template] to see a bare-bones
example of an app. The full API documentation, generated from the python source
code, can be found [here][api].

[app-template]: https://github.com/OPSORO/OS/tree/master/src/opsoro/apps/app_template
[api]: http://docs.opsoro.be/en/master/
[repo]: https://github.com/opsoro/os
[flask]: http://flask.pocoo.org
[fdn]: http://foundation.zurb.com
[jq]: https://jquery.com
[ko]: http://knockoutjs.com

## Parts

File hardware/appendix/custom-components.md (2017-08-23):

# List of custom components
This document contains an overview of all the custom parts used in the Opsoro
system. Nearly all custom parts are fabricated using either laser-cutting or
3D-printing, and the hierarchy of this document reflects this.

## Laser-cut components
Laser-cutting is used extensively in the hardware design of Opsoro. Most parts
are cut from 3 mm ABS plastic. Most parts can be connected using the
snap connectors, meaning no extra fasteners are required.

### Button module
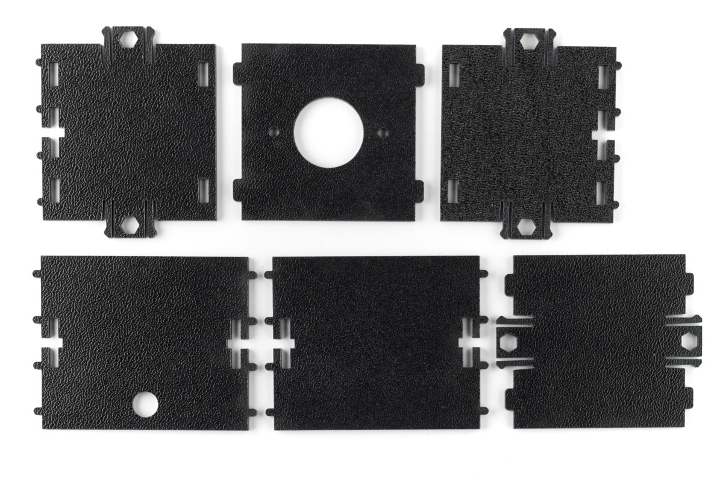
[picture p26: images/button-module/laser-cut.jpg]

Cut from 3mm ABS plastic. Source file can be found [here](https://github.com/OPSORO/BUILD/blob/master/modules/button/button_module.3dm).

### Turn module
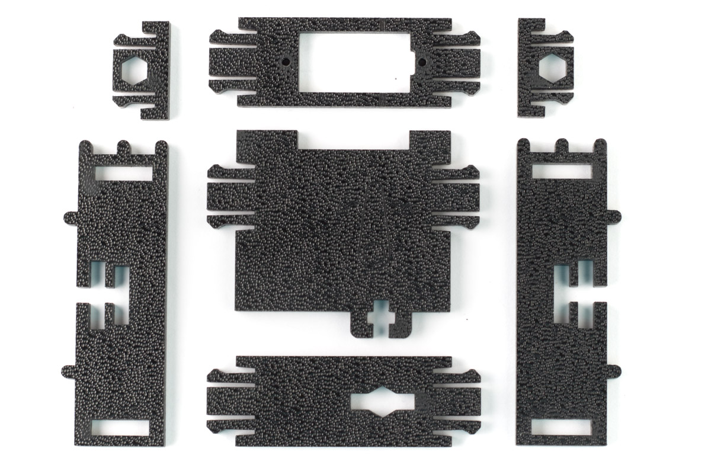
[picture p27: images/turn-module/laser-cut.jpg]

Cut from 3mm ABS plastic. Source file can be found [here](https://github.com/OPSORO/BUILD/blob/master/modules/turn/turn_module.3dm).

### Eye module
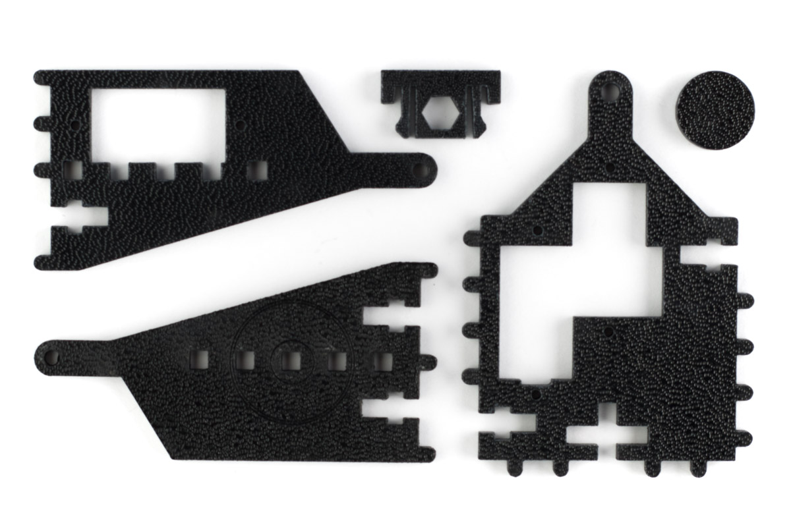
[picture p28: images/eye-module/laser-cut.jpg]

Cut from 3mm ABS plastic. Source file can be found [here](https://github.com/OPSORO/BUILD/blob/master/modules/eye/eye_module.3dm).

### Heart module

### LED matrix module
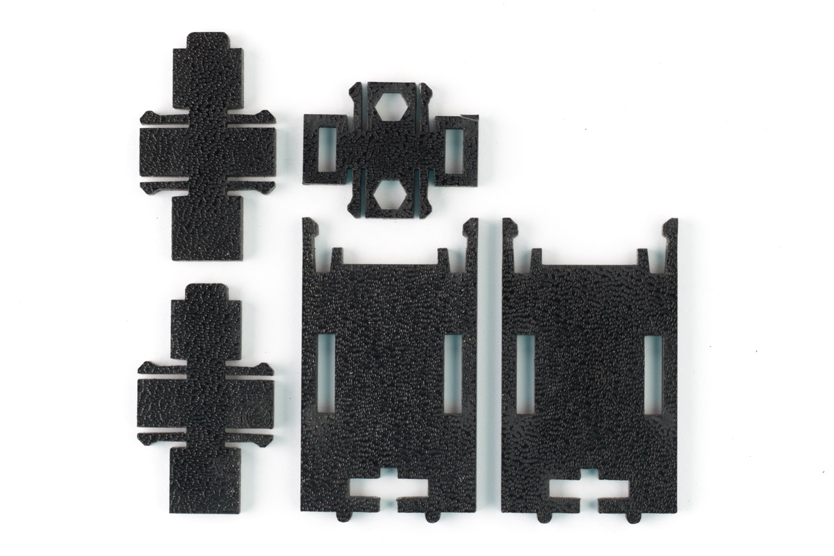
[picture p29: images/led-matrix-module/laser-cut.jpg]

Cut from 3mm ABS plastic. Source file can be found [here](https://github.com/OPSORO/BUILD/blob/master/modules/matrix/matrix_module_new.3dm).

### Motion sensor module
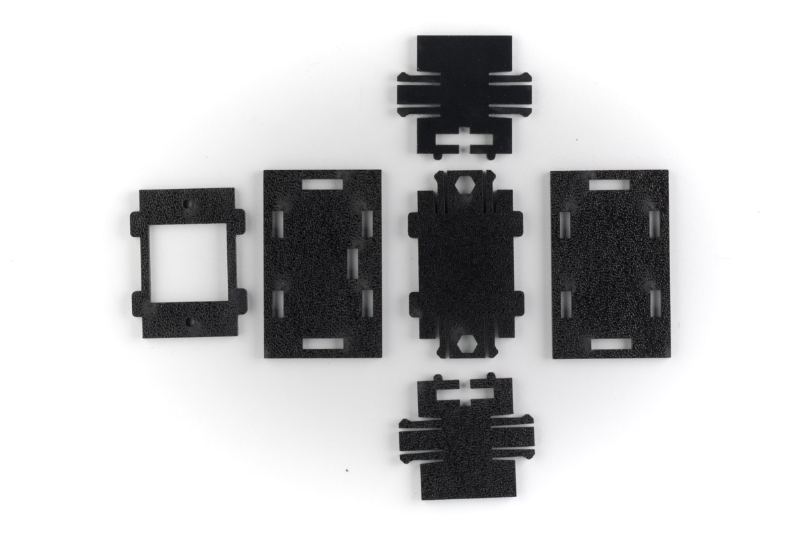
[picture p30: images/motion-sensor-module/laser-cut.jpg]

Cut from 3mm ABS plastic. Source file can be found [here](https://github.com/OPSORO/BUILD/blob/master/modules/pir-motion/pir-motion.3dm).

### Speaker module
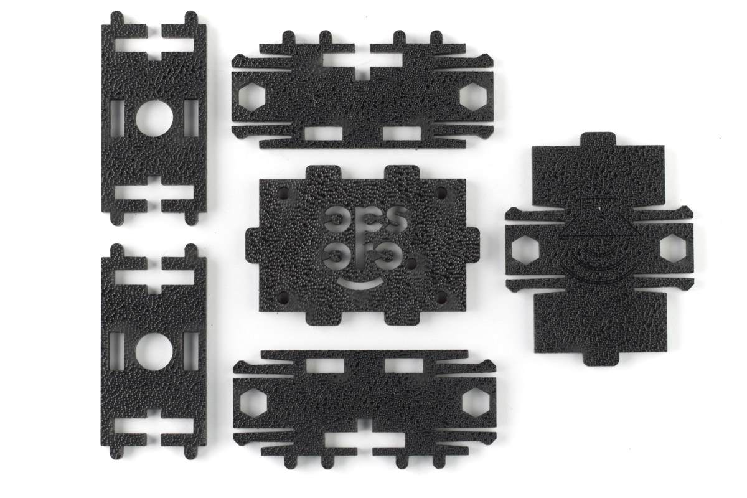
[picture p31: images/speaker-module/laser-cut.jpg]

Cut from 3mm ABS plastic. Source file can be found [here](https://github.com/OPSORO/BUILD/blob/master/modules/speaker/speaker_module.3dm).

### Camera module
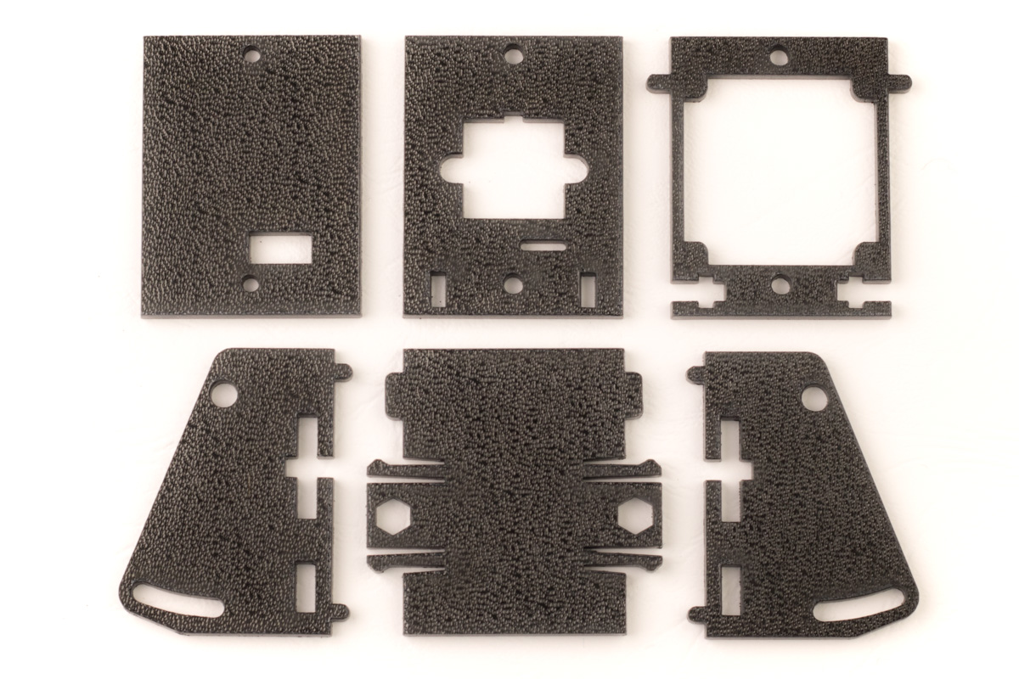
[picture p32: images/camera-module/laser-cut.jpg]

Cut from 3mm ABS plastic. Source file can be found [here](https://github.com/OPSORO/BUILD/blob/master/modules/camera/camera.3dm).

## 3D-printed components
Some parts of the Opsoro system are 3D printed using a hobby-grade 3D printer.
We print our parts on Ultimaker 2 machines, but the parts are designed so that
they could be printed on most low-end FDM machines. The 3D printed parts usually
have some small artifacts, such as stringing and blobs. These can be removed
using flush cutters. Holes in 3D printed parts usually require some cleanup as
well. Go through the holes with a small drill to clear any debris. Most holes
are 3 mm in size, and can be cleaned up using a 3 mm drill.

### Eye shell
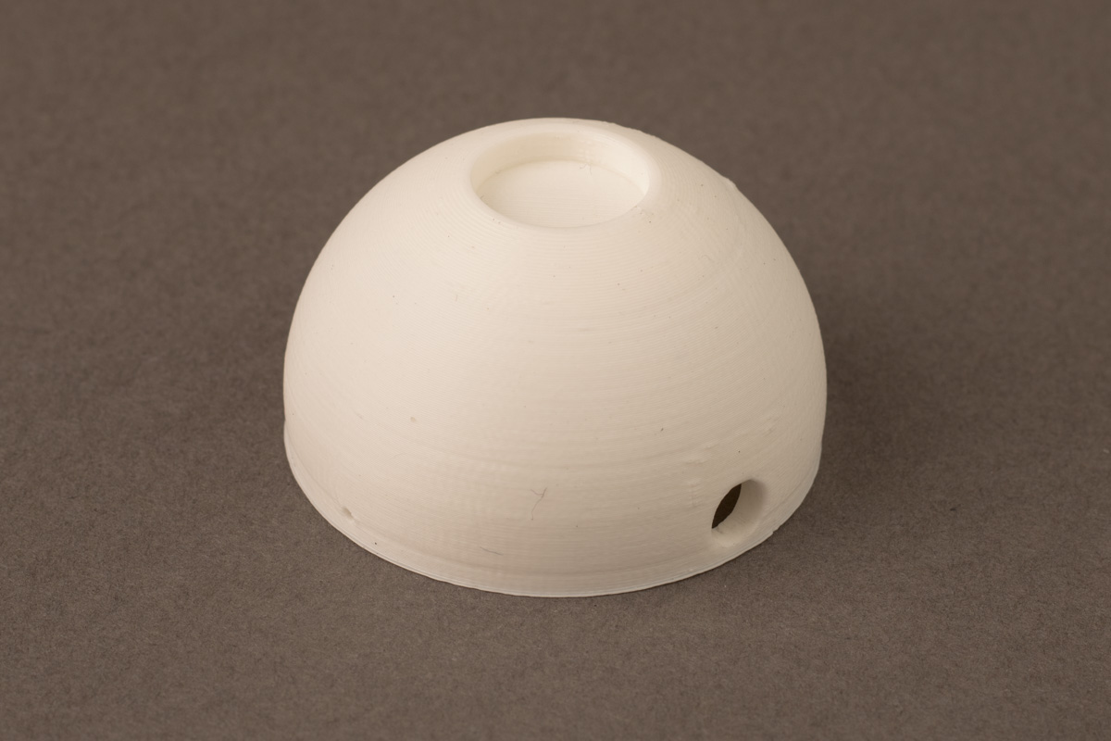
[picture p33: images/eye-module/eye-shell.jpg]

Printed in white PLA plastic. Source file can be found [here](https://github.com/OPSORO/BUILD/blob/master/modules/eye/shell.stl).

### Eyelid

Printed in white PLA plastic. Source file can be found [here](https://github.com/OPSORO/BUILD/blob/master/modules/eye/lid.stl).

### Pivot beam

Printed in white PLA plastic. Source file can be found [here](https://github.com/OPSORO/BUILD/blob/master/modules/eye/pivot_beam.stl).

## Printed circuit boards

### LED matrix PCB

Prototype. Source file can be found [here](https://github.com/OPSORO/BUILD/tree/master/modules/matrix/led-matrix-proto).

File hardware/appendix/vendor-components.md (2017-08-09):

#List of vendor components
This article gives an overview of all the off-the-shelf components used in
the Opsoro system.

## Mechanical components

### Fasteners

| Description | Price | Purchase link |
|---|---|---|
| M3x6 hex socket cap screw (DIN 912)  | €5,49 (100pcs) | [Conrad][m3x6] |
| M3x10 hex socket cap screw (DIN 912) | €5,49 (100pcs) | [Conrad][m3x10] |
| M3 nut | €3,79 (100pcs) | [Conrad][m3 nut] |
| M3 washer | €1,99 (100pcs) | [Conrad][m3 washer]  |

[m3x6]: http://www.conrad.be/ce/nl/product/839667
[m3x10]: http://www.conrad.be/ce/nl/product/839669
[m3 nut]: http://www.conrad.be/ce/nl/product/1060794
[m3 washer]: http://www.conrad.be/ce/nl/product/521619

## Electrical components

### Raspberry Pi
| Description | Price | Purchase link |
|---|---|---|
| Raspberry Pi 3 model B | €37,99 | [Farnell][rpi] |
| Micro SD card (8 GB) | - | - |

[rpi]: http://be.farnell.com/raspberry-pi/raspberrypi3-modb-1gb/sbc-raspberry-pi-3-mod-b-1gb-ram/dp/2525225

### Speaker
| Description | Price | Purchase link |
|---|---|---|
| Mini speaker (4 W, 4 ohm) | €4,51 | [Farnell][speaker] |

[speaker]: http://be.farnell.com/pro-signal/abs-230-rc/speaker-miniature-4ohm-4w/dp/1867858

### DuPont connectors
| Description | Price | Purchase link |
|---|---|---|
| Crimp contacts | €0.53 (10pcs)  | [Farnell][crimp] |
| Connector housing - 2 positions | €0.08 | [Farnell][2pos] |
| Connector housing - 2x3 positions | €0.24 | [Farnell][2x3pos] |
| Female Crimp Header kit | €15,95 | [iPrototype][dupont-kit] |

[2pos]: http://be.farnell.com/multicomp/2226a-02/crimp-housing-1-row-2-way/dp/1593506
[2x3pos]: http://be.farnell.com/multicomp/2226b-06/crimp-housing-2-row-6way/dp/1593520
[crimp]: http://be.farnell.com/multicomp/2226tg/crimp-terminal-24-28awg/dp/1593529
[dupont-kit]: https://www.iprototype.nl/products/accessoires/headers/female-crimp-headers

### KK 254 connectors
| Description | Price | Purchase link |
|---|---|---|
| Crimp contacts | €0.30 (10pcs)  | [Farnell][kkcrimp] |
| Connector housing - 2 positions | €0.09 | [Farnell][kk2pos] |

[kk2pos]: http://be.farnell.com/multicomp/2218t/contact-crimp-plug-26-22awg-cut/dp/1675781
[kkcrimp]: http://be.farnell.com/multicomp/2226tg/crimp-terminal-24-28awg/dp/1593529

### Servos
| Description | Price | Purchase link |
|---|---|---|
| Servo extension cable M-F (300mm) | &plusmn; €4,00 (10pcs) | [AliExpress][ext-cable] |
| Micro metal-gear servo MG90S | &plusmn; €1,50 | [AliExpress][micro]  |

[micro]: https://www.aliexpress.com/wholesale?catId=0&initiative_id=SB_20170801021307&SearchText=mg90s
[ext-cable]: https://www.aliexpress.com/wholesale?catId=0&initiative_id=AS_20170801021308&SearchText=servo+extension+300mm

### Power supply
| Description | Price  | Purchase link |
|---|---|---|
| Power supply 5V/7A - 35W - 2.1MM DC PLUG | €18,95 | [Kiwi][psu] |
| 2.1mm DC barrel jack (F) - panel mount | €1,95  | [Kiwi][barrel] |

[psu]: http://www.kiwi-electronics.nl/Power-Adapter-5V-7A-DC-35-Watt-100-240-AC-EU-kabel
[barrel]: https://www.kiwi-electronics.nl/2.1mm-dc-barrel-jack-panel-mount

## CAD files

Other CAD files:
images/grid/grid-dimensions.3dm

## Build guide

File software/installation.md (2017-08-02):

# Installation

There are two ways to install OpsoroOS on your Raspberry Pi. The recommended
option is to flash the precompiled disk image to an SD card and use that with
your Pi. It is also possible to install the necessary software manually. This
might be necessary if you want to install the software on an existing
installation. This option is intended for advanced users.

## Precompiled disk image

A precompiled disk image is available for Raspberry Pi. This disk image is based
on Raspbian Jessie (lite) and contains all the necessary software to run
OpsoroOS. The image is compatible with the Raspberry Pi 1, 2, 3, and Zero. The
disk image can be downloaded **here**. The disk image cannot be copied to the SD
card directly, it needs to be flashed via a special utility. The process is
explained on [this page][disk-image].

[disk-image]: https://www.raspberrypi.org/documentation/installation/installing-images/

> **Warning** While the disk image contains all the necessary dependencies, the
> main python software might be slightly out of date. After flashing the disk
> image, it is recommended to update the software via the *Preferences* page.

## Manual installation

Manual installation of the software is also possible, though the process is more
involved. Make sure your Raspberry Pi can connect to the internet and connect to
the device via SSH.

1. Start with a fresh Raspbian install
2. Copy the contents the folder /OnoSW/ to /home/pi/OnoSW/
3. Copy the contents the folder /Scripts/ to /home/pi/Scripts/
4. Update your system

    ```
    sudo apt-get update
    sudo apt-get upgrade
    ```
5. Install Python development files, Avahi daemon, LuaJIT

    ```
    sudo apt-get install python2.7-dev avahi-daemon libluajit-5.1-dev
    ```

6. Install PIP

    ```
    sudo apt-get install python-setuptools
    sudo easy_install pip
    ```

7. [Compile and install LibYAML](http://pyyaml.org/wiki/LibYAML)  
    Or run following command:  
    ```
    sudo apt-get install python-yaml
    ```

    This step is not strictly necessary, but will result in a massive speedup
    when parsing config files. The python version of PyYAML takes well over 3
    seconds to parse the configs, the C version takes only a fraction of that.

8. Install Python packages (flask, flask-login, pyyaml, pluginbase, sockjs-tornado, simplejson, lupa, numpy, scipy, spidev)

    ```
    sudo pip install flask flask-login pyyaml pluginbase sockjs-tornado simplejson lupa numpy spidev
    sudo apt-get install -y python-smbus i2c-tools
    sudo apt-get install -y python-scipy
    ```

9. Enable SPI and I2C

    ```
    sudo raspi-config
    ```

    Go to advanced, A5 SPI --> Enable, A6 --> I2C enable.

10. Edit /etc/modules

    ```
    sudo nano /etc/modules
    ```

    Enter the following configuration

    ```
    # /etc/modules: kernel modules to load at boot time.
    #
    # This file contains the names of kernel modules that should be loaded
    # at boot time, one per line. Lines beginning with "#" are ignored.
    # Parameters can be specified after the module name.

    #snd-bcm2835
    i2c-bcm2708
    i2c-dev
    snd_soc_core
    snd_soc_bcm2708_i2s
    bcm2708_dmaengine
    snd_soc_pcm1794a
    snd_soc_rpi_dac
    ```
    Edit /etc/modprobe.d/raspi-blacklist.conf and make the file is empty. (no modules blacklisted)  

    ```
    sudo nano /etc/modprobe.d/raspi-blacklist.conf
    ```
11. Configure audio
    Add hifiberry-dac device tree overlay in config.txt
    (```sudo nano /boot/config.txt```). And add the following to the end of the
    config.txt file
    ```
    dtoverlay=hifiberry-dac
    ```
    If present, change ```dtparam=audio=on``` to ```#dtparam=audio=on```

    Configure ALSA

    ```
    sudo nano /etc/asound.conf
    ```

    Enter the following configuration

    ```
    pcm.!default {
      type        softvol
      slave.pcm   dac
      control {
        name      "Master"
        card      0
      }
    }

    pcm.dac {
      type plug
      slave {
        pcm       "hw:0,0"
        format     S16_LE
        channels   2
        rate       48000
      }
    }
    ```

    Reboot the Raspberry Pi

    ```
    sudo reboot
    ```

    Lower the master sound volume to something reasonable (limits 0-255)

    ```
    amixer set Master 128
    ```

12. [Install PicoTTS][pico]

    ```
    sudo apt-get install libttspico-utils
    ```

13. Install the eSpeak TTS engine

    ```
    sudo apt-get install espeak
    ```

14. Setup and configure the WiFi dongle  
    Install hostapd for the access point and dnsmasq for the DHCP server and DNS redirect

    ```
    sudo apt-get install -y hostapd dnsmasq
    ```

    Update ```/etc/network/interfaces``` so it matches following lines

    ```
    auto lo
    iface lo inet loopback

    allow-hotplug eth0
    iface eth0 inet manual

    #allow-hotplug wlan0
    #iface wlan0 inet manual
    #    wpa-conf /etc/wpa_supplicant/wpa_supplicant.conf

    #allow-hotplug wlan1
    #iface wlan1 inet manual
    #    wpa-conf /etc/wpa_supplicant/wpa_supplicant.conf

    allow-hotplug wlan0
    auto wlan0
    iface wlan0 inet static
       address 192.168.42.1
       netmask 255.255.255.0
       broadcast 192.168.42.255

    # reset existing rules and chains
    up /sbin/iptables -F
    up /sbin/iptables -X
    up /sbin/iptables -t nat -F

    # Mask for the interface, activate port-forwarding and NAT
    up iptables -A FORWARD -o eth0 -i wlan0 -s 192.168.42.0/24 -m conntrack --ctstate NEW -j ACCEPT
    up iptables -A FORWARD -m conntrack --ctstate ESTABLISHED,RELATED -j ACCEPT

    up iptables -t nat -A POSTROUTING -o eth0 -j MASQUERADE
    up sysctl -w net.ipv4.ip_forward=1

    # restart hostapd and dnsmasq
    up /etc/init.d/hostapd restart
    up /etc/init.d/dnsmasq restart
    ```

    Use the following configuration for /etc/hostapd/hostapd.conf

    ```
    interface=wlan0
    driver=nl80211
    ssid=OpSoRo_Robot
    ieee80211n=1          # 802.11n support
    wmm_enabled=1         # QoS support
    ht_capab=[HT40][SHORT-GI-20][DSSS_CCK-40]
    hw_mode=g
    channel=6
    macaddr_acl=0
    auth_algs=1
    ignore_broadcast_ssid=0
    wpa=2
    wpa_key_mgmt=WPA-PSK
    wpa_passphrase=opsoro123
    rsn_pairwise=CCMP
    ```

    Edit the file /etc/default/hostapd and change the line ```#DAEMON_CONF=""```
    to ```DAEMON_CONF="/etc/hostapd/hostapd.conf"```.

    Configure the DHCP server and DNS redirect.
    Create new config file (```sudo nano /etc/dnsmasq.d/dnsmasq.opsoro.conf```)
    and paste following lines:

    ```
    # Redirect specific urls
    address=/play.opsoro.be/192.168.42.1

    # DHCP-Server active for the wlan interface
    interface=wlan0

    # IP-Address range / Lease-Time
    dhcp-range=interface:wlan0,192.168.42.100,192.168.42.200,infinite
    ```

15. Change the host name to "opsoro"  
    In the files "/etc/hostname" and "/etc/hosts", change "raspberrypi" to 
    "opsoro"

    ```
    sudo nano /etc/hostname
    sudo nano /etc/hosts
    ```

16. Setup Opsoro service  
    The script for setting up opsoro can be found in /Scripts/.  
    Follow next steps to setup OpSoRo

    ```
    sudo cd /home/pi/Scripts/
    sudo chmod +x setup_opsoro
    sudo ./setup_opsoro
    ```

The Opsoro software and its dependencies should now all be installed and
working. Reboot the Raspberry Pi to test. Please [let us know][github-issue] if
any steps are missing!

[github-issue]: https://github.com/OPSORO/OS/issues/new
[pico]: http://rpihome.blogspot.be/2015/02/installing-pico-tts.html

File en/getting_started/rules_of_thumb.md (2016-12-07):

# Rules of Thumb

We've defined a couple of rules in order to help you in making robots more easily.

1. ####Standard & Digital Parts
OPSORO is designed using (1) only standard parts that can easily be found/bought online or in any DIY shop and (2) digital files that can be used to 3D-print, laser-cut or cnc-mill any other OPSORO parts locally. If any part of your robot would break 
   
2. ####Voltage & Danger

3. ####Software

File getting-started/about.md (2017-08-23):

# About OPSORO
Opsoro originated at [Ghent University][ugent] in Belgium. This research is
part of the department of [Industrial Systems and Product Design][ea18] and the
[UGent Industrial Design Center][idc]. Academic publications on the Opsoro
project can be found on [ResearchGate][rg].

[ugent]: https://www.ugent.be
[ea18]: https://ea18.ugent.be/
[idc]: https://ea18.ugent.be/research/IDC
[rg]: https://www.researchgate.net/project/OPSORO

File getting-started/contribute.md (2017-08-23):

# Contribute

Our mission with Opsoro is to offer an open platform that enables everyone to
create their own social robots. Want to help us achieve this goal? We welcome
collaboration efforts and contributions! Here are some things we could use your
help with:

* Create new apps
* Contribute features and fixes to Opsoro-OS
* Design custom hardware modules
* Share your custom robot designs with us
* Help us improved the documentation

Don't forget to get in touch with us to tell us about your work!
You can contact us by [email](mailto:info@opsoro.be), via
[facebook](http://www.facebook.com/opsoro), or on the
[forum](https://www.opsoro.be/forum/).

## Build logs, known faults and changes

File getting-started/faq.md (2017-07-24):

# Frequently Asked Questions

<!-- toc -->

##### Can I use OPSORO if there is no WiFi available?
Yes. When not connected to the internet, you can use OPSORO in 'local'mode. This means that the heart will function as a hot-spot and emit a WiFi signal all by itself.

##### Can I use OPSORO if I don't have any OPSORO hardware?
Yes. Go to our website www.opsoro.be and navigate to the tab 'Play'. After registration you will have access to the online platform, where you can display a virtual robot model.

##### Can I use Arduino or other 3rd party equipment/sensors?
Yes. The OPSORO shield gives you the ability to connect all kinds of different 3rd party equipment like: temperature sensors, makey makeys, arduinos, ...

##### Is it easy to make my own skin?
Yes, depending on the level of detail you want to put into it. A cardboard 2D skin is typically made in less than 2 hours (from age 6). A Lasered skin can be designed and prototyped in 1 day (from age 16). You should at least calculate a full-time week to design a 3D textile robot (16+).

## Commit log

2017-02-23 Updates installation/raspberry_pi.md
    Auto commit by GitBook Editor
2017-07-24 Updates modules/skin-design/laser-cutting.md
    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
2017-07-25 Added new template for module assembly instructions
2017-07-27 Added grid documentation
    [grid-dimensions.3dm]
2017-07-31 Updated appendix with servo info
2017-08-01 Added servo timing diagram
2017-08-01 Updated assembly template with model variable
2017-08-02 Added KK 254 connectors
2017-08-02 Added bill-of-materials and tools for all modules
2017-08-02 Initial version of embodiments BOM
2017-08-07 Motion sensor assembly instructions
2017-08-08 LED matrix documentation
2017-08-09 Button assembly documentation
2017-08-09 Added servo centering instructions
2017-08-09 Added details on eye bom
2017-08-22 Added eye assembly instructions
2017-08-23 Added camera module documentation
2017-08-23 Added logo to landing page
